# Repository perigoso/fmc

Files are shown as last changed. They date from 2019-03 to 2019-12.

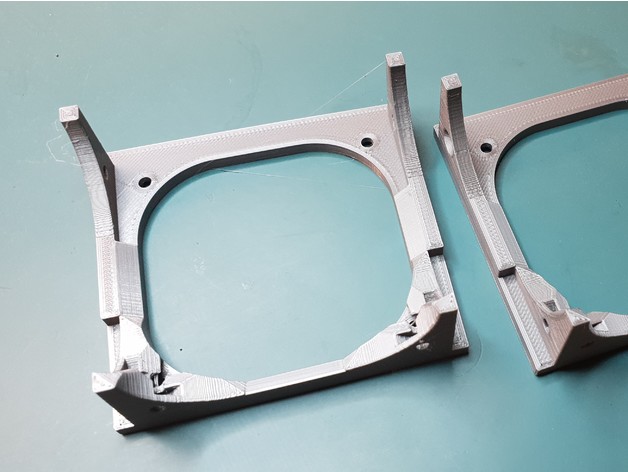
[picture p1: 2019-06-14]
hardware/mech/images/d837dd31dcf635642381db13449b711e_preview_featured.jpg

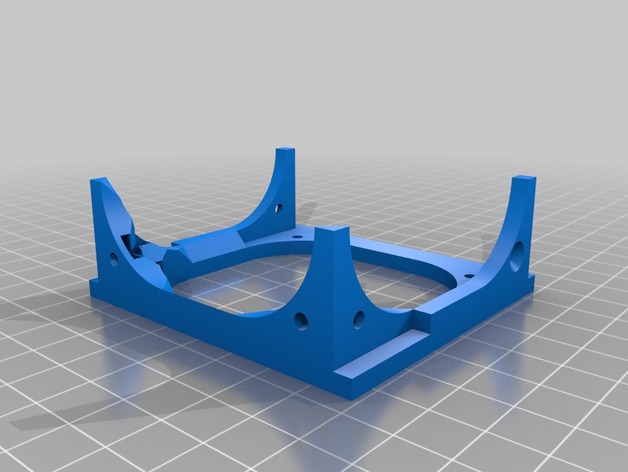
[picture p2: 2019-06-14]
hardware/mech/images/b15bb7bc5afcf96a0e5b0992fa541031_preview_featured.jpg

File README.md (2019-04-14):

# ipl motion controller

Flexible BLDC, Stepper, DC motor controller with position torque and speed control

## Authors

* **Rafael Silva** - [gimbas](https://github.com/crying-face-emoji)

See also the list of [contributors](https://github.com/gimbas/cp2130/graphs/contributors) who participated in this project.

## License

This project is licensed under the GNU General Public License v3.0 - see the [LICENSE.md](LICENSE.md) file for details

## Acknowledgments

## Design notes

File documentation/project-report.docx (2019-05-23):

Project Report

For

BLDC Motion Controller

Representative image

Company name

Date
11-Apr-19

Table of Contents

Document structure and summary

# Introduction

# Project Scope

# Project Members

Schedule Baseline and Work Breakdown

# Milestones

# Cost Breakdown

# Annotated Bibliography

- Features / system overview
- Funcional description / theory of operation
- Diagrama de blocos
- Componentes utilizados (i fix it style)
- Descrição funcionamento de componentes
- Interface / modo de controlo
- Getting started / example
- Register maps / descriptions
- Eletrical caracteristics
- Conector identification / specs

10/04/2019 - Document criation

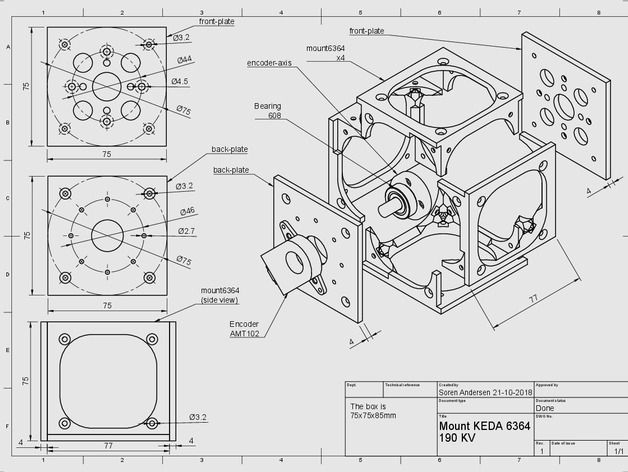
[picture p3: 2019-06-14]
hardware/mech/images/94975ee713d6cb6adc06fc9739ce1cb8_preview_featured.jpg

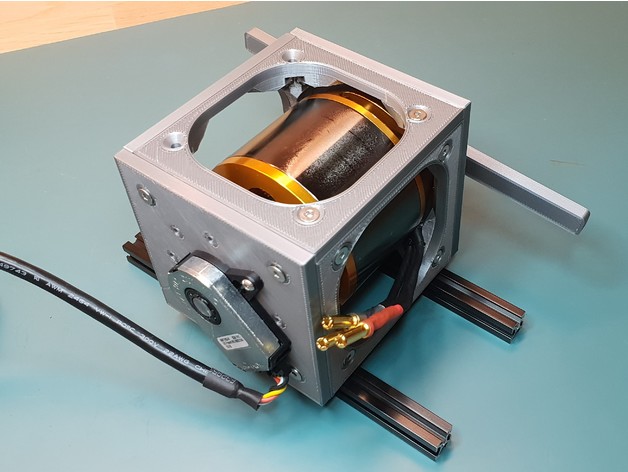
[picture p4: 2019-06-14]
hardware/mech/images/7b22074a1c9e0729f0604e04f04d98aa_preview_featured.jpg

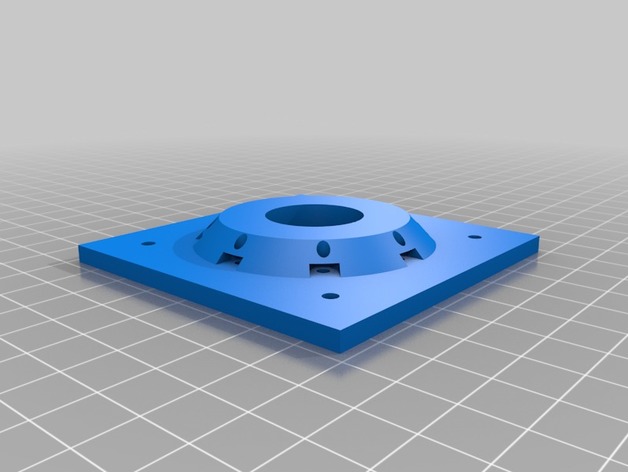
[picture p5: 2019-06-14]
hardware/mech/images/675c46c8c70f695663abe5cd2488d6a1_preview_featured.jpg

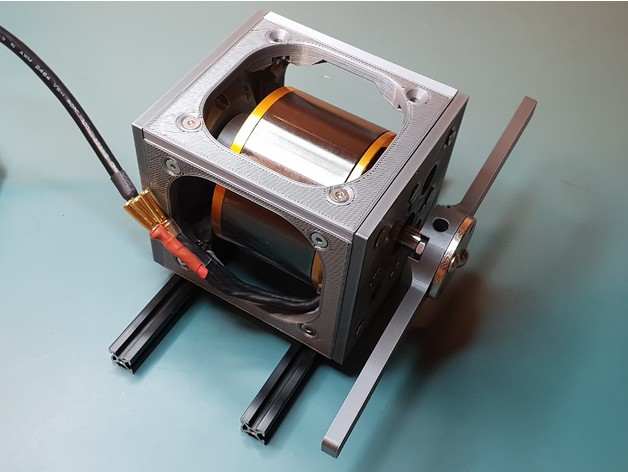
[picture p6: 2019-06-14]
hardware/mech/images/bdaeb86baf7d3e5aeb2ae743f0c55633_preview_featured.jpg

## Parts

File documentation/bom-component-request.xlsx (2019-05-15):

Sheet: Mouser
Name | Manufacturer | Reference | Description | Comments | Quantity | Link
Encoder | CUI Inc. | AMT102-V | (Kit) Rotary Encoder Incremental Programmable Quadrature with Index 2048 CPR | - | 2 | https://eu.mouser.com/ProductDetail/CUI/AMT102-V?qs=%2Fha2pyFadui4RzVBRTfUG9UOa9jox1ECIM3vJaJgYZM%3D
Schmitt Trigger Buffer | Nexperia | 74LVC3G17DP,125 | Inverters TRIP NO-INV SCH TRIG | - | 5 | https://eu.mouser.com/ProductDetail/Nexperia/74LVC3G17DP125
Headers | Hirose Connector | DF20F-10DP-1V | Headers & Wire Housings 10P M PIN HEADER DR STRAIGHT SMT GOLD | - | 1 | https://eu.mouser.com/ProductDetail/798-DF20F10DP1V55
Terminals | Phoenix Contact | 1706756 | Fixed Terminal Blocks MKDSV 5/ 4-6.35 32A | - | 3 | https://eu.mouser.com/ProductDetail/Phoenix-Contact/1710056?qs=sGAEpiMZZMvZTcaMAxB2ABBNmx7J9ErWGaY6GpdlOPw%3D
Terminals | Phoenix Contact | 1710056 | Fixed Terminal Blocks MKDSV 5/ 2-6.35 32A | - | 1 | https://eu.mouser.com/ProductDetail/Phoenix-Contact/1710056?qs=sGAEpiMZZMvZTcaMAxB2ABBNmx7J9ErWGaY6GpdlOPw%3D
Schottky Diodes | ROHM Semiconductor | BAT54SHMFHT116 | Schottky Diodes & Rectifiers 30V Vr 0.2A Io SBD SOT-23 0.1A | - | 10 | https://eu.mouser.com/ProductDetail/755-BAT54SHMFHT116
Mosfets | Infineon / IR | IRF7580MTRPBF | MOSFET 60V StrongIRFET Power Mosfet | - | 15 | https://eu.mouser.com/ProductDetail/Infineon-IR/IRF7580MTRPBF
Schottky Diodes | MCC | B5817w | Schottky Diodes & Rectifiers 1A Schottky Rectifier | - | 5 | https://eu.mouser.com/ProductDetail/833-B5817W-TP
Sense Resistors | Bourns | LRMAP3920B-R0007FT | Current Sense Resistors - SMD 1.0mOHMS 8W 1% AEC-Q200 | - | 2 | https://eu.mouser.com/ProductDetail/Bourns/CSS2H-3920R-1L00FE
NTC | Murata | NCU18WF104J60RB | NTC (Negative Temperature Coefficient) Thermistors 100kohm 1608 SMD 0.05 | - | 2 | https://eu.mouser.com/ProductDetail/Murata-Electronics/NCU18WF104J60RB
Resistors | Yageo | RC0603FR-07100RL | Thick Film Resistors 100 OHM 1% | - | 100 | https://eu.mouser.com/ProductDetail/Yageo/RC0603FR-07100RL?qs=sGAEpiMZZMvdGkrng054txdMlaQGj9fiaLtoULAqhv0%3D
Resistors | Yageo | RC0603FR-074K22L | Thick Film Resistors 4.22K OHM 1% | - | 10 | https://eu.mouser.com/ProductDetail/Yageo/RC0603FR-074K22L
Resistors | Yageo | RC0603FR-072R2L | Thick Film Resistors 2.2 OHM 1% | - | 20 | https://eu.mouser.com/ProductDetail/Yageo/RC0603FR-072R2L?qs=sGAEpiMZZMvdGkrng054t8AJgcdMkx7xQlq9a62Wvu8%3D
Resistors | Yageo | RC0603FR-0710KL | Thick Film Resistors 10K OHM 1% | - | 100 | https://eu.mouser.com/ProductDetail/Yageo/RC0603FR-0710KL
Resistors | Yageo | RC0603FR-07100KL | Thick Film Resistors 100K OHM 1% | - | 100 | https://eu.mouser.com/ProductDetail/Yageo/RC0603FR-07100KL
Capacitors | KEMET | C0603C104Z3VACTU | Multilayer Ceramic Capacitors MLCC - SMD/SMT 25V 0.1uF 0603 Y5V -20/+80% | - | 50 | https://eu.mouser.com/ProductDetail/KEMET/C0603C104Z3VACTU?qs=sGAEpiMZZMvsSlwiRhF8qiamir66WTSkBwWGHarofks%3D
Capacitors | Wurth Electronics | 885012206077 | Multilayer Ceramic Capacitors MLCC - SMD/SMT WCAP-CSGP 100pF 0603 10% 50V | - | 50 | https://eu.mouser.com/ProductDetail/Wurth-Electronics/885012206077
Capacitors | Taiyo Yuden | TMK107BJ224KAHT | Multilayer Ceramic Capacitors MLCC - SMD/SMT 0.22uF 25V X5R +/-10% 0603 AEC-Q200 | - | 5 | https://eu.mouser.com/ProductDetail/963-TMK107BJ224KAHT
Inductor | Pulse Electronics | PA4342.683ANLT | Fixed Inductors 68uH 2.4A 4mm 20% SMT | - | 2 | https://eu.mouser.com/ProductDetail/Pulse-Electronics/PA4342683ANLT
Capacitors | Lelon | VZL101M1ETR-0607 | Aluminium Electrolytic Capacitors - SMD 100uF 25 Volts 20% | - | 5 | https://eu.mouser.com/ProductDetail/Lelon/VZL101M1ETR-0607
Capacitors | Nichicon | UWT1H221MNL1GS | Aluminium Electrolytic Capacitors - SMD 50volts 220uF 10x10 '20% | - | 5 | https://eu.mouser.com/ProductDetail/Nichicon/UWT1H221MNL1GS?qs=sGAEpiMZZMtZ1n0r9vR22RxmuzErLMSVGlVEB2AeLYo%3D

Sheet: Digikey
Name | Manufacturer | Reference | Description | Comments | Quantity | Link
Motor Controller | Trinamic | TMC4671-ES | Motor Field Oriented Controller, BLDC, DC Motor, PMSM, Stepper | - | 3 | https://www.digikey.com/products/en?keywords=TMC4671-ES
Programmer cable | TagConnect | TC2050-IDC-NL-ND | Programmers Accessories | - | 1 | https://www.digikey.com/product-detail/en/tag-connect-llc/TC2050-IDC-NL/TC2050-IDC-NL-ND/2605367
tc cable clip | TagConnect | TC2050-CLIP-ND | Programmers Accessories | - | 1 | https://www.digikey.com/product-detail/en/tag-connect-llc/TC2050-CLIP/TC2050-CLIP-ND/2605374

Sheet: HobbyKing
Name | Manufacturer | Reference | Description | Comments | Quantity | Link
BLDC | KEDA | KEDA 63-64 190KV | KEDA 63-64 190KV Brushless Outrunner 10S 2000W | - | 1 | https://hobbyking.com/pt_pt/kd-53-30-high-voltage-brushless-outrunner-190kv.html

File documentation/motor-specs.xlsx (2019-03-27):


Name | Manufacturer | Reference | Hall effect | Nphase | Npole (N+S) | Stator Slots | Cogging steps / turn | velocity constant (Kv) | Ke | Kt | Imax | Pmax | Vmax | I0 (No load current) | Ri (Winding res) | Inductance | Tq | Rpm | Price | Weigth | Shaft | Body Length | Body width
KEDA 63-64 190KV Brushless Outrunner 10S 2000W | KEDA |  | N | 3 | 14 | 12 | 84 | 190 | 0.005263 | 0.005263 | 90 A | 2000 W | 37 V |  | 0 | 0 | 0.474 Nm | 4921 rpm | 45.46€ | 670g | d8mm l25mm | 66mm | 63mm
 |  |  |  |  | Copper Loss = Amps² × Rm Iron Loss = Volts × Io Motor Losses = Copper loss + Iron Loss Power In = Volts × Amps Power Out = Power In − All Losses Efficiency = Power Out / Power In Kt = 1/Kv (SI units: with RPM in rad/sec) Torque = Kt × Amps Km = Kt / sqrt(Rm)
 |  |  |  |  | Kv = RPM / (Volts × 1.414 × 0.95)
 |  |  |  |  | Kv = RPM / (Volts − Amps × Rm)

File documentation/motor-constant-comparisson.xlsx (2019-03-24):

Motor
Name | Manufacturer | reference | Sensored | kv | ke | kt | rated current | rated power | rated voltage | max torque | max rpm aproximation | price
Turnigy CA120 150kv Brushless Outrunner (100cc equiv) | Turnigy |  | N | 150 | 0.006667 | 0.006667 | 250 A | 15000 W | 70 V | 1.667 Nm | 7350 rpm | 303.19€
Turnigy RotoMax 150cc Size Brushless Outrunner Motor | Turnigy |  | N | 150 | 0.006667 | 0.006667 | 190 A | 9800 W | 52 V | 1.267 Nm | 5460 rpm | 0.00€
Turnigy CA80 160kv Brushless Outrunner (50~80cc Eq) | Turnigy |  | N | 160 | 0.006250 | 0.006250 | 200 A | 10000 W | 50 V | 1.250 Nm | 5600 rpm | 147.74€
Turnigy RotoMax 100cc Size Brushless Outrunner Motor 167kv | Turnigy |  | N | 167 | 0.005988 | 0.005988 | 170 A | 7992 W | 44 V | 1.018 Nm | 5143.6 rpm | 300.16€
Turnigy RotoMax 50cc Size Brushless Outrunner Motor | Turnigy |  | N | 172 | 0.005814 | 0.005814 | 120 A | 5300 W | 44 V | 0.698 Nm | 5297.6 rpm | 199.24€
9235-100KV Turnigy Multistar Brushless Multi-Rotor Motor | Turnigy |  | N | 100 | 0.010000 | 0.010000 | 57 A | 2800 W | 45 V | 0.570 Nm | 3150 rpm | 93.00€
Turnigy SK8 6374-149KV Sensored Brushless Motor (14P) | Turnigy |  | Y | 149 | 0.006711 | 0.006711 | 80 A | 3500 W | 44 V | 0.537 Nm | 4589.2 rpm | 86.06€
Turnigy SK8 6374-192KV Sensored Brushless Motor (14P) | Turnigy |  | Y | 192 | 0.005208 | 0.005208 | 100 A | 4400 W | 45 V | 0.521 Nm | 6048 rpm | 85.90€
Turnigy SK8 6374-130KV Sensored Brushless Motor (14P) | Turnigy |  | Y | 130 | 0.007692 | 0.007692 | 65 A | 2800 W | 45 V | 0.500 Nm | 4095 rpm | 85.69€
KEDA 63-64 190KV Brushless Outrunner 10S 2000W | KEDA |  | N | 190 | 0.005263 | 0.005263 | 90 A | 2000 W | 37 V | 0.474 Nm | 4921 rpm | 45.46€
Turnigy Aerodrive SK3 - 6374-149KV Brushless Outrunner Motor | Turnigy |  | N | 149 | 0.006711 | 0.006711 | 70 A | 2250 W | 44 V | 0.470 Nm | 4589.2 rpm | 86.21€
Turnigy Aerodrive SK3 - 6374-168KV Brushless Outrunner Motor | Turnigy |  | N | 168 | 0.005952 | 0.005952 | 70 A | 2400 W | 44 V | 0.417 Nm | 5174.4 rpm | 74.88€
Turnigy Aerodrive SK3 - 6374-192KV Brushless Outrunner Motor | Turnigy |  | N | 192 | 0.005208 | 0.005208 | 80 A | 2750 W | 44 V | 0.417 Nm | 5913.6 rpm | 74.77€
KEDA 56-63 195KV Brushless Outrunner 6S 1500W | KEDA |  | N | 195 | 0.005128 | 0.005128 | 80 A | 1500 W | 22 V | 0.410 Nm | 3003 rpm | 36.92€
9225-90KV Turnigy Multistar Brushless Multi-Rotor Motor | Turnigy |  | N | 90 | 0.011111 | 0.011111 | 36 A | 1200 W | 45 V | 0.400 Nm | 2835 rpm | 148.72€
Turnigy SK8 6364-110KV Sensored Brushless Motor (14P) | Turnigy |  | Y | 110 | 0.009091 | 0.009091 | 40 A | 1750 W | 45 V | 0.364 Nm | 3465 rpm | 80.39€
Turnigy D5035-125KV Sensored Brushless Motor | Turnigy |  | Y | 125 | 0.008000 | 0.008000 | 45 A | 2000 W | 44 V | 0.360 Nm | 3850 rpm | 91.41€
Turnigy RotoMax 1.60 Brushless Outrunner Motor | Turnigy |  | N | 231 | 0.004329 | 0.004329 | 80 A | 2960 W | 37 V | 0.346 Nm | 5982.9 rpm | 121.94€
Turnigy Aerodrive SK3 - 6364-190KV Brushless Outrunner Motor | Turnigy |  | N | 190 | 0.005263 | 0.005263 | 65 A | 2450 W | 37 V | 0.342 Nm | 4921 rpm | 78.97€
PROPDRIVE v2 5060 270KV Brushless Outrunner Motor | PROPDRIVE |  | N | 270 | 0.003704 | 0.003704 | 90 A | 2400 W | 30 V | 0.333 Nm | 5670 rpm | 49.94€
Turnigy SK8 6364-245KV Sensored Brushless Motor (14P) | Turnigy |  | Y | 245 | 0.004082 | 0.004082 | 80 A | 3500 W | 45 V | 0.327 Nm | 7717.5 rpm | 80.39€
Turnigy SK8 6364-190KV Sensored Brushless Motor (14P) | Turnigy |  | Y | 190 | 0.005263 | 0.005263 | 60 A | 2600 W | 45 V | 0.316 Nm | 5985 rpm | 80.39€
Turnigy Aerodrive SK3 - 6364-213KV Brushless Outrunner Motor | Turnigy |  | N | 213 | 0.004695 | 0.004695 | 65 A | 2550 W | 37 V | 0.305 Nm | 5516.7 rpm | 66.09€
9225-160KV Turnigy Multistar Brushless Multi-Rotor Motor | Turnigy |  | N | 160 | 0.006250 | 0.006250 | 48 A | 1200 W | 35 V | 0.300 Nm | 3920 rpm | 93.00€
Turnigy SK8 6354-140KV Sensored Brushless Motor (14P) | Turnigy |  | Y | 140 | 0.007143 | 0.007143 | 42 A | 1850 W | 45 V | 0.300 Nm | 4410 rpm | 71.06€
Turnigy Aerodrive SK3 - 6364-245Kv Brushless Outrunner Motor | Turnigy |  | N | 245 | 0.004082 | 0.004082 | 70 A | 2700 W | 37 V | 0.286 Nm | 6345.5 rpm | 70.57€
Turnigy SK8 6354-200KV Sensored Brushless Motor (14P) | Turnigy |  | Y | 200 | 0.005000 | 0.005000 | 55 A | 2420 W | 45 V | 0.275 Nm | 6300 rpm | 71.14€
Turnigy Aerodrive SK3 - 6354-260KV Brushless Outrunner Motor | Turnigy |  | N | 260 | 0.003846 | 0.003846 | 70 A | 2360 W | 37 V | 0.269 Nm | 6734 rpm | 67.20€
Turnigy SK8 6354-260KV Sensored Brushless Motor (14P) | Turnigy |  | Y | 260 | 0.003846 | 0.003846 | 70 A | 3000 W | 45 V | 0.269 Nm | 8190 rpm | 70.66€
Turnigy G160 Brushless Outrunner 290kv (160 Glow) | Turnigy |  | N | 290 | 0.003448 | 0.003448 | 78 A | 2700 W | 37 V | 0.269 Nm | 7511 rpm | 84.26€
Turnigy Aerodrive SK3 - 5065-236Kv Brushless Outrunner Motor | Turnigy |  | N | 236 | 0.004237 | 0.004237 | 60 A | 1850 W | 37 V | 0.254 Nm | 6112.4 rpm | 61.32€
PROPDRIVE v2 5060 380KV Brushless Outrunner Motor | PROPDRIVE |  | N | 380 | 0.002632 | 0.002632 | 90 A | 2665 W | 36 V | 0.237 Nm | 9576 rpm | 42.13€
Turnigy Aerodrive SK3 - 5065-275KV Brushless Outrunner Motor | Turnigy |  | N | 275 | 0.003636 | 0.003636 | 65 A | 2050 W | 37 V | 0.236 Nm | 7122.5 rpm | 53.16€
Turnigy Aerodrive SK3 - 5065-320kv Brushless Outrunner Motor | Turnigy |  | N | 320 | 0.003125 | 0.003125 | 70 A | 2220 W | 37 V | 0.219 Nm | 8288 rpm | 56.64€
Turnigy G60 Brushless Outrunner 300kv (.60 Glow) | Turnigy |  | N | 300 | 0.003333 | 0.003333 | 65 A | 1425 W | 26 V | 0.217 Nm | 5460 rpm | 50.08€
Turnigy Aerodrive SK3 - 5055-280KV Brushless Outrunner Motor | Turnigy |  | N | 280 | 0.003571 | 0.003571 | 60 A | 1510 W | 37 V | 0.214 Nm | 7252 rpm | 53.02€
Turnigy Aerodrive SK3 - 5055-320Kv Brushless Outrunner Motor | Turnigy |  | N | 320 | 0.003125 | 0.003125 | 65 A | 1650 W | 37 V | 0.203 Nm | 8288 rpm | 53.11€
Turnigy Aerodrive SK3 - 5055-380KV Brushless Outrunner Motor | Turnigy |  | N | 380 | 0.002632 | 0.002632 | 65 A | 1600 W | 37 V | 0.171 Nm | 9842 rpm | 43.29€
Turnigy Aerodrive SK3 - 5055-430KV Brushless Outrunner Motor | Turnigy |  | N | 430 | 0.002326 | 0.002326 | 70 A | 1750 W | 30 V | 0.163 Nm | 9030 rpm | 46.03€
Turnigy G60 Brushless Outrunner 400kv (.60 Glow) | Turnigy |  | N | 400 | 0.002500 | 0.002500 | 65 A | 1009 W | 26 V | 0.163 Nm | 7280 rpm | 53.29€
Turnigy Aerodrive SK3 - 4250-350KV Brushless Outrunner Motor | Turnigy |  | N | 350 | 0.002857 | 0.002857 | 53 A | 1190 W | 19 V | 0.151 Nm | 4655 rpm | 34.04€
Turnigy Aerodrive SK3 - 4250-410KV Brushless Outrunner Motor | Turnigy |  | N | 410 | 0.002439 | 0.002439 | 55 A | 1310 W | 19 V | 0.134 Nm | 5453 rpm | 34.04€
Turnigy G46 Brushless Outrunner 420kv (.46 Glow) | Turnigy |  | N | 420 | 0.002381 | 0.002381 | 55 A | 925 W | 19 V | 0.131 Nm | 5586 rpm | 46.44€
4112-320KV Turnigy Multistar 22 Pole Brushless Multi-Rotor Motor With Extra Long Leads | Turnigy |  | N | 320 | 0.003125 | 0.003125 | 20 A | 660 W | 30 V | 0.062 Nm | 6720 rpm | 37.18€
Multistar Elite 3508-268kv Multi-Rotor Motor with NMB Bearings | Turnigy |  | N | 268 | 0.003731 | 0.003731 | 16 A | 400 W | 22.2 V | 0.060 Nm | 4164.72 rpm | 31.12€
4010-375KV Turnigy Multistar 22 Pole Brushless Multi-Rotor Motor With Extra Long Leads | Turnigy |  | N | 375 | 0.002667 | 0.002667 | 20 A | 450 W | 25 V | 0.053 Nm | 6562.5 rpm | 38.49€
Quanum MT Series 5206 320KV Brushless Multirotor Motor Built by DYS | DYS |  | N | 320 | 0.003125 | 0.003125 | 17 A | 384 W | 22 V | 0.053 Nm | 4928 rpm | 33.50€
Quanum MT Series 4108 370KV Brushless Multirotor Motor Built by DYS | DYS |  | N | 370 | 0.002703 | 0.002703 | 16 A | 355 W | 22 V | 0.043 Nm | 5698 rpm | 30.38€
Multistar Elite 3510-350kv Carbon Case Multi-Rotor Motor | Turnigy |  | N | 350 | 0.002857 | 0.002857 | 15 A | 330 W | 22 V | 0.043 Nm | 5390 rpm | 35.35€
Turnigy Multistar 4822-390Kv 22Pole Multi-Rotor Outrunner | Turnigy |  | N | 390 | 0.002564 | 0.002564 | 15 A | 300 W | 22 V | 0.038 Nm | 6006 rpm | 34.22€
Turnigy Multistar 4225-390Kv 16Pole Multi-Rotor Outrunner | Turnigy |  | N | 390 | 0.002564 | 0.002564 | 15 A | 330 W | 22 V | 0.038 Nm | 6006 rpm | 31.77€
 |  |  |  |  | #DIV/0! | #DIV/0! |  |  |  | #DIV/0! | 0 rpm | 0.00€

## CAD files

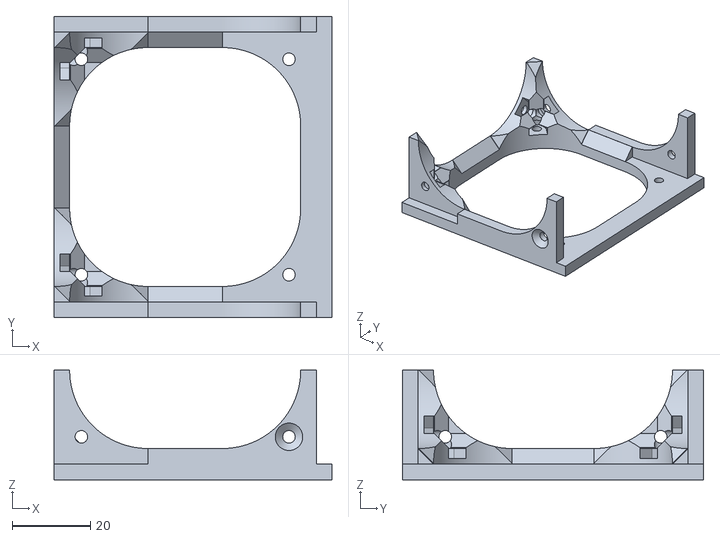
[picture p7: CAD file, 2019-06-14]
hardware/mech/files/v25-mount6364-rotated.stl
71.0 x 77.0 x 28.0

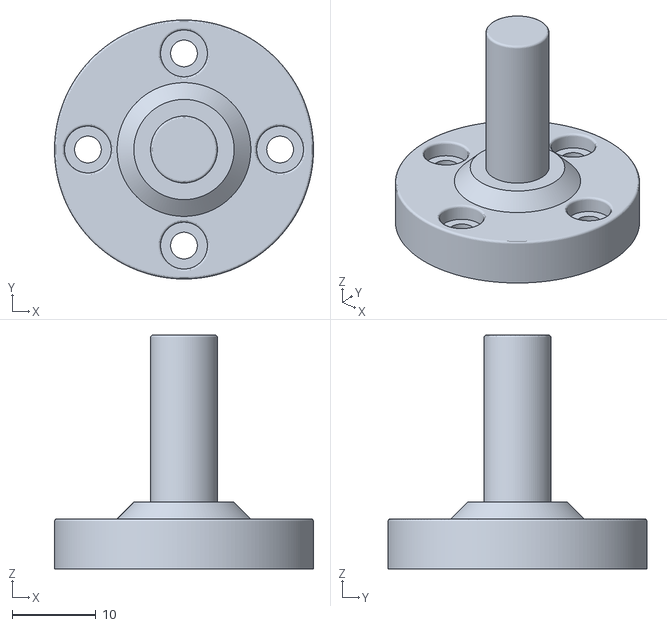
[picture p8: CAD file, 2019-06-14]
hardware/mech/files/v25-encoder-axis.stl
31.0 x 31.0 x 28.0

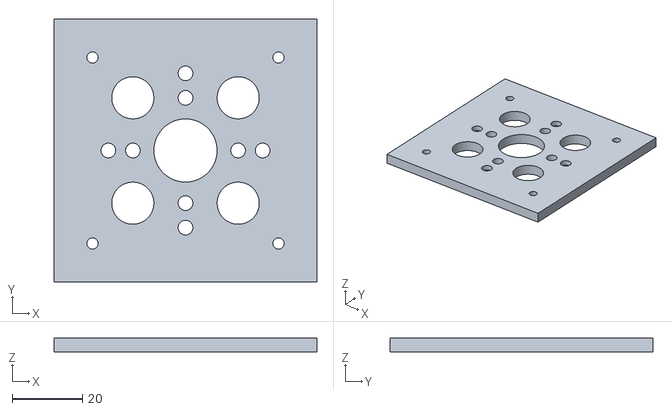
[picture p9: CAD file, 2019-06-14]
hardware/mech/files/v25-front-plate.stl
75.0 x 75.0 x 4.00

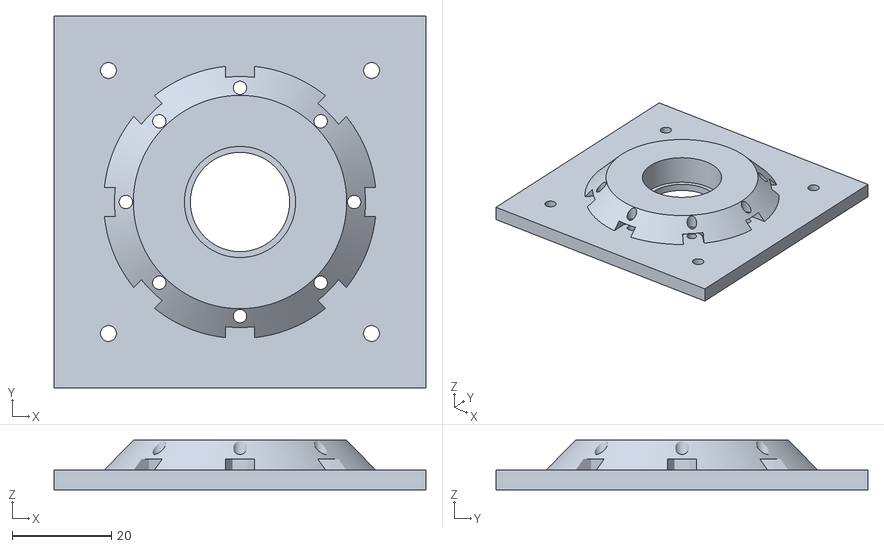
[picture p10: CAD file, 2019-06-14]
hardware/mech/files/v25-back-plate-rotated.stl
75.0 x 75.0 x 10.0

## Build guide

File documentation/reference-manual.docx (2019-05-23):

Project Report

For

BLDC Motion Controller

Representative image

Company name

Date
11-Apr-19

Table of Contents

# Introduction

# Project Scope

# Project Members

# Milestones

- Capa
- About this document
- Table of Contents
- Introdução
- Features / system overview
- Funcional description / theory of operation
- Diagrama de blocos
- Componentes utilizados (i fix it style)
- Descrição funcionamento de componentes
- Interface / modo de controlo
- Getting started / example
- Register maps / descriptions
- Eletrical caracteristics
- Conector identification / specs
- Revision history
- “Bibliografia”

10/04/2019 - Document criation

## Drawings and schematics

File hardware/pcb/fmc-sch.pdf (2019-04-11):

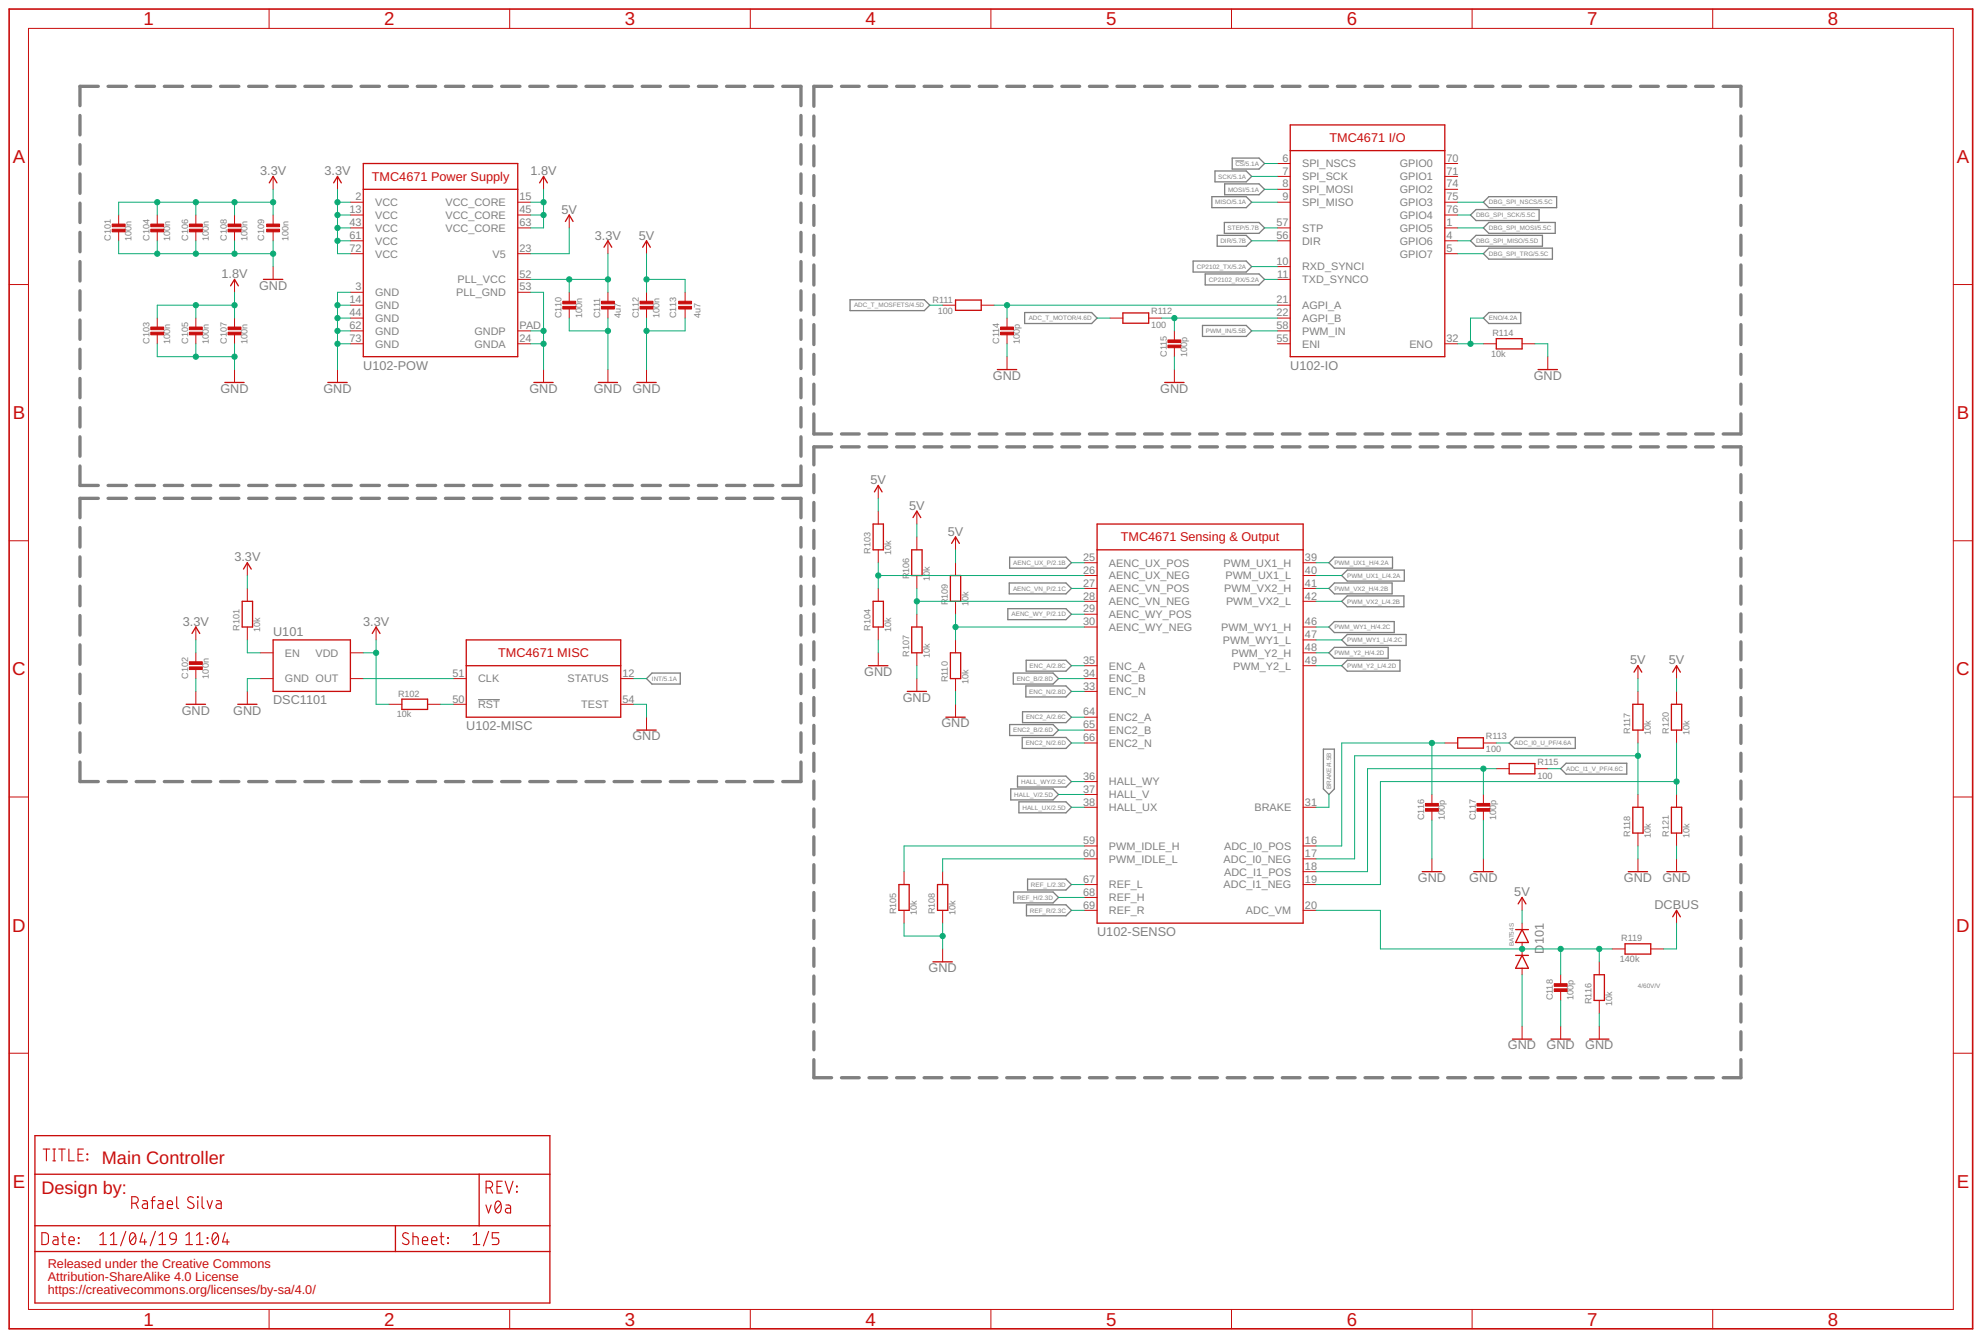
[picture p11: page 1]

13 | 45
43 | 63
61 | 23

14 | PAD

Released under the Creative Commons https://creativecommons.org/licenses/by-sa/4.0/
Attribution-ShareAlike 4.0 License

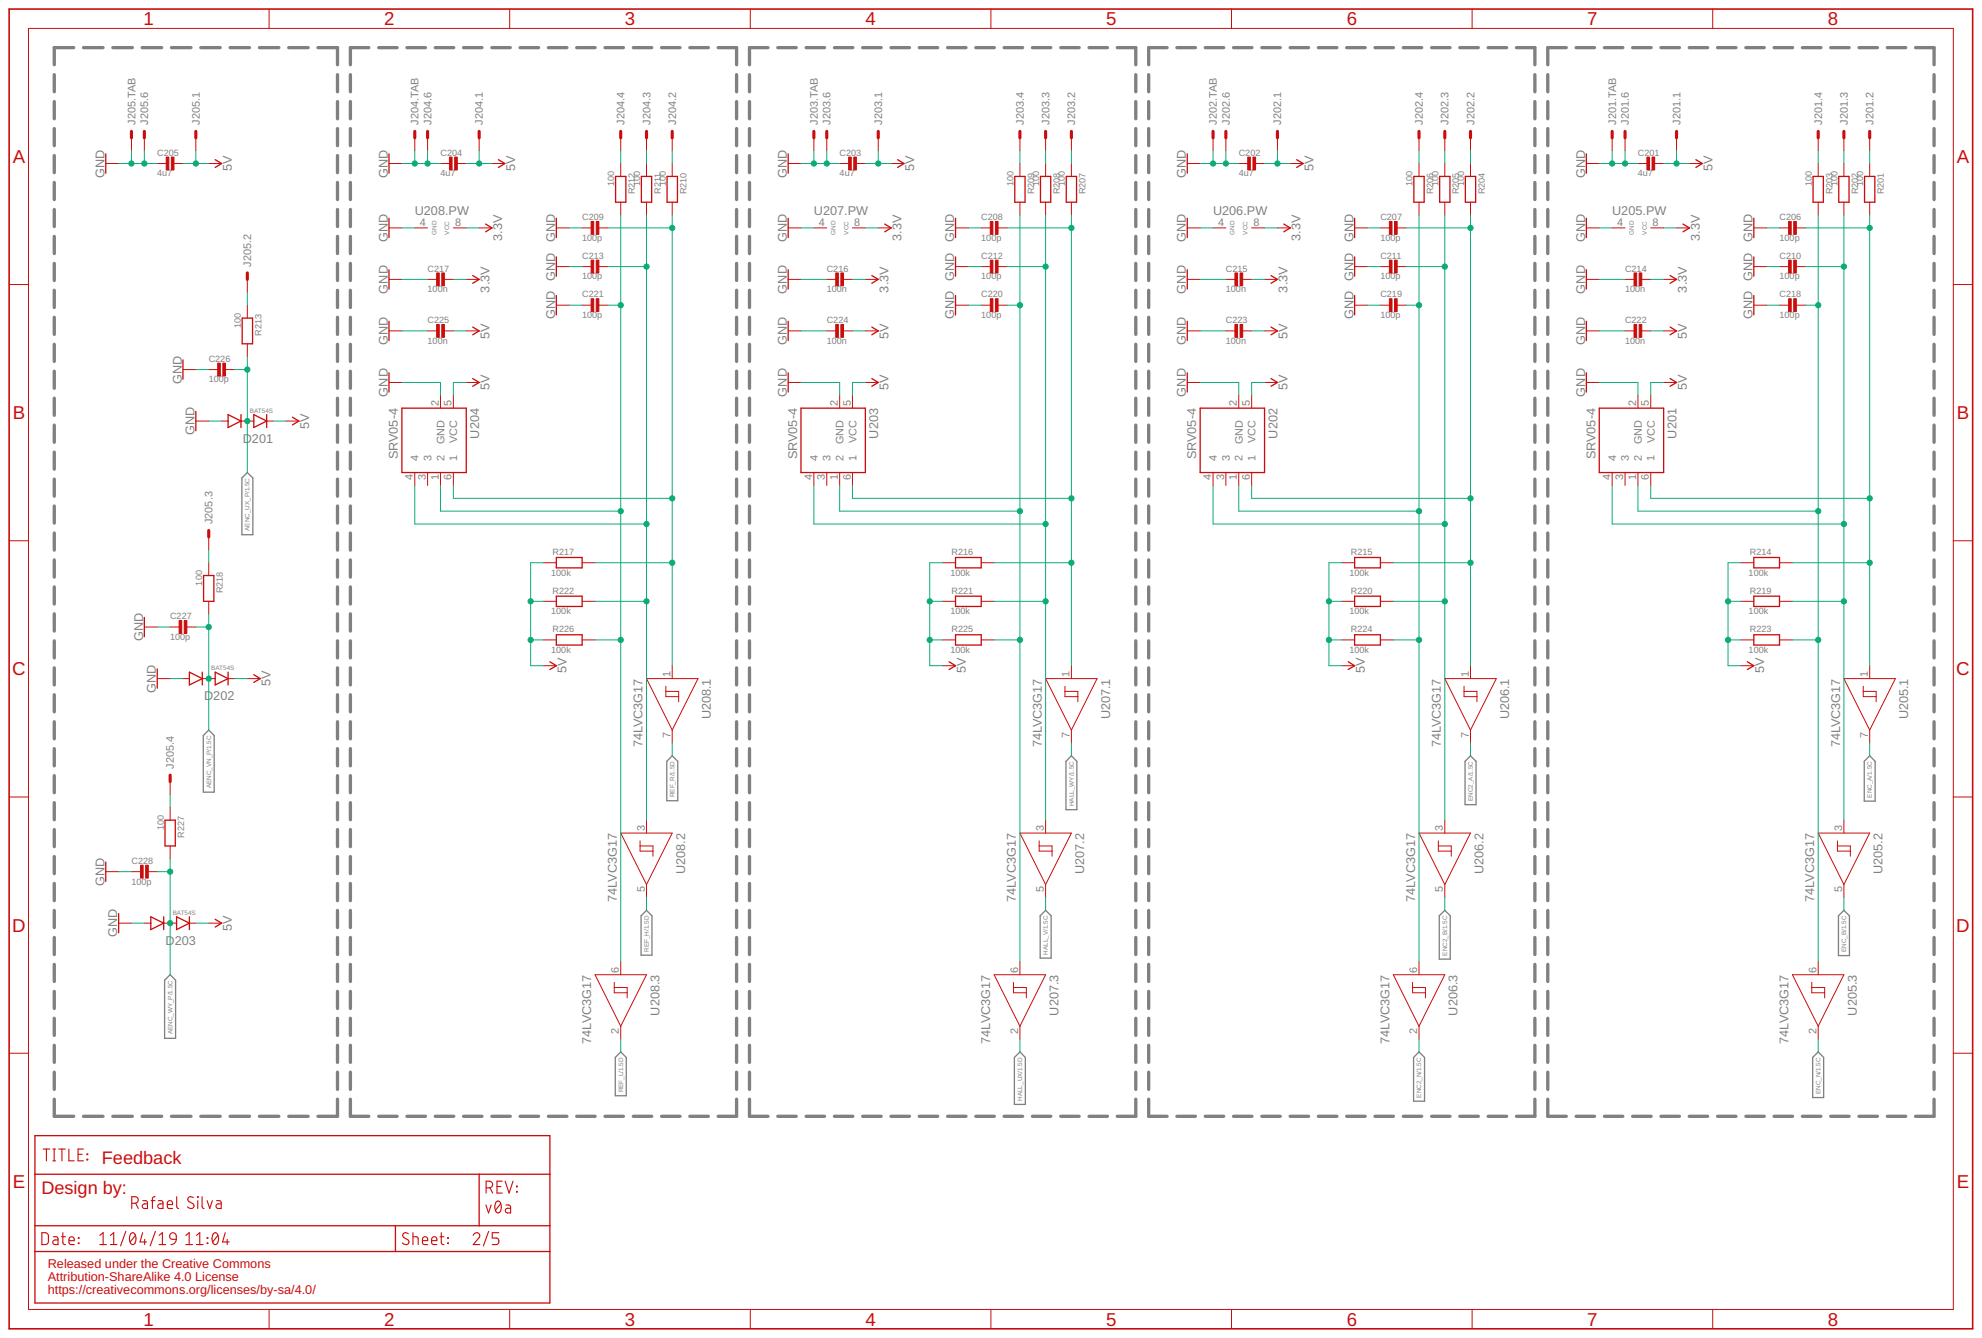
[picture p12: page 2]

VCC GND VCC GND VCC GND VCC GND 74LVC3G17 74LVC3G17 74LVC3G17 100 100 100 100p 100p 100p 4u7 5V GND GND GND GND GND 5V GND 74LVC3G17 74LVC3G17 74LVC3G17 100 100 100 100p 100p 100p 4u7 5V GND GND GND GND GND 5V GND 74LVC3G17 74LVC3G17 74LVC3G17 100 100 100 100p 100p 100p 4u7 5V GND GND GND GND GND 5V GND 100n 5V GND 3.3V 3.3V G100n ND 3.3V 100n 5V GND G100n ND 3.3V 3.3V 100k 100k 100k5V 100k 100k 100k5V 100k 100k 100k5V 100n 5V GND G100n ND 3.3V 74LVC3G17 74LVC3G17 74LVC3G17 100 100 100 100p 100p 100p 4u7 5V GND GND GND GND GND 5V GND 100n 5V GND G100n ND 3.3V 3.3V 100k 100k 100k5V BAT54S BAT54S BAT54S 100p 100p 100p 100 100 100 4u7 5V GND GND GND GND 5V 5V 5V GND GND GND SRV05-4 SRV05-4 SRV05-4 SRV05-4 1 7 U205.1 3 5 U205.2 6 2 U205.3 4 8 U205.PW J201.1 J201.2 J201.3 J201.4 J201.6 J201.TAB R201 R202 R203 C206 C210 C218 C201 1 7 U206.1 3 5 U206.2 6 2 U206.3 4 8 U206.PW J202.1 J202.2 J202.3 J202.4 J202.6 J202.TAB R204 R205 R206 C207 C211 C219 C202 1 7 U207.1 3 5 U207.2 6 2 U207.3 4 8 U207.PW J203.1 J203.2 J203.3 J203.4 J203.6 J203.TAB R207 R208 R209 C208 C212 C220 C203 C223 C215 C224 C216 R216 R221 R225 R215 R220 R224 R214 R219 R223 C222 C214 1 7 U208.1 3 5 U208.2 6 2 U208.3 4 8 U208.PW J204.1 J204.2 J204.3 J204.4 J204.6 J204.TAB R210 R211 R212 C209 C213 C221 C204 C225 C217 R217 R222 R226 D201 D202 D203 C226 C227 C228 R213 R218 R227 C205 J205.1 J205.2 J205.3 J205.4 J205.6 J205.TAB VCC 5 GND 2 1 6 2 1 3 3 4 4 U202 VCC 5 GND 2 1 6 2 1 3 3 4 4 U201 VCC 5 GND 2 1 6 2 1 3 3 4 4 U203 VCC 5 GND 2 1 6 2 1 3 3 4 4 U204 ENC2_A/1.5C ENC2_B/1.5C ENC2_N/1.5C HALL_WY/1.5C HALL_V/1.5C HALL_UX/1.5D ENC_A/1.5C ENC_B/1.5C ENC_N/1.5C REF_R/1.5D REF_H/1.5D REF_L/1.5D AENC_UX_P/1.5C AENC_VN_P/1.5C AENC_WY_P/1.5C Feedback ABCDE 1 2 3 4 5 6 7 8 ABCDE 1 2 3 4 5 6 7 8 Design by: Released under the Creative Commons https://creativecommons.org/licenses/by-sa/4.0/ Attribution-ShareAlike 4.0 License

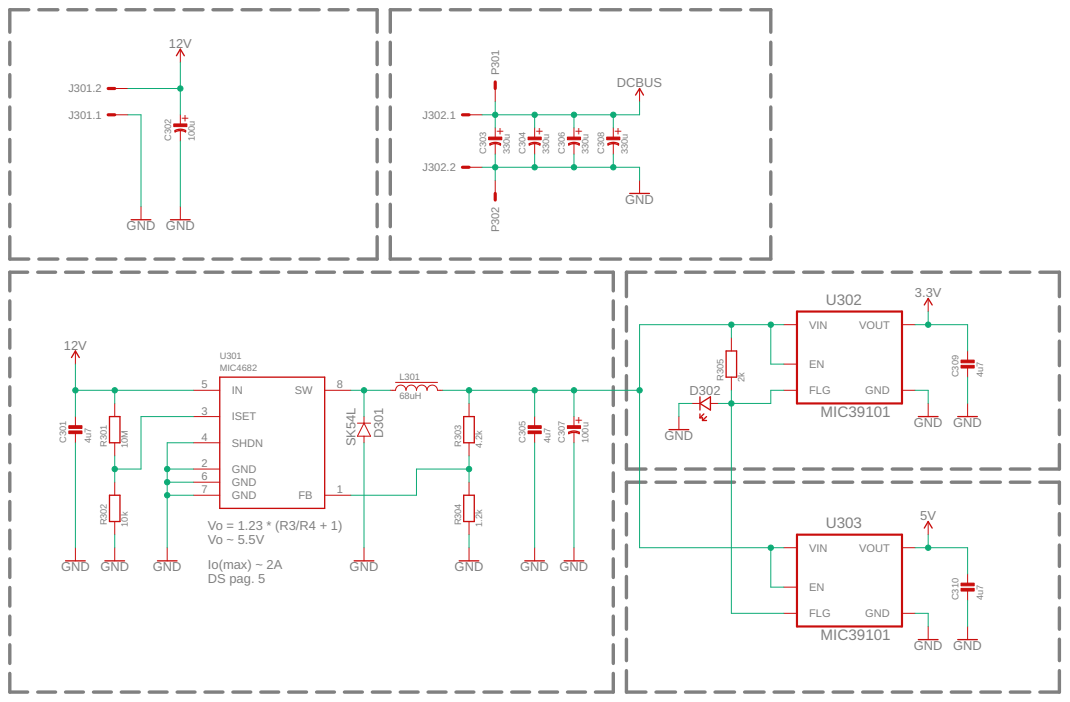
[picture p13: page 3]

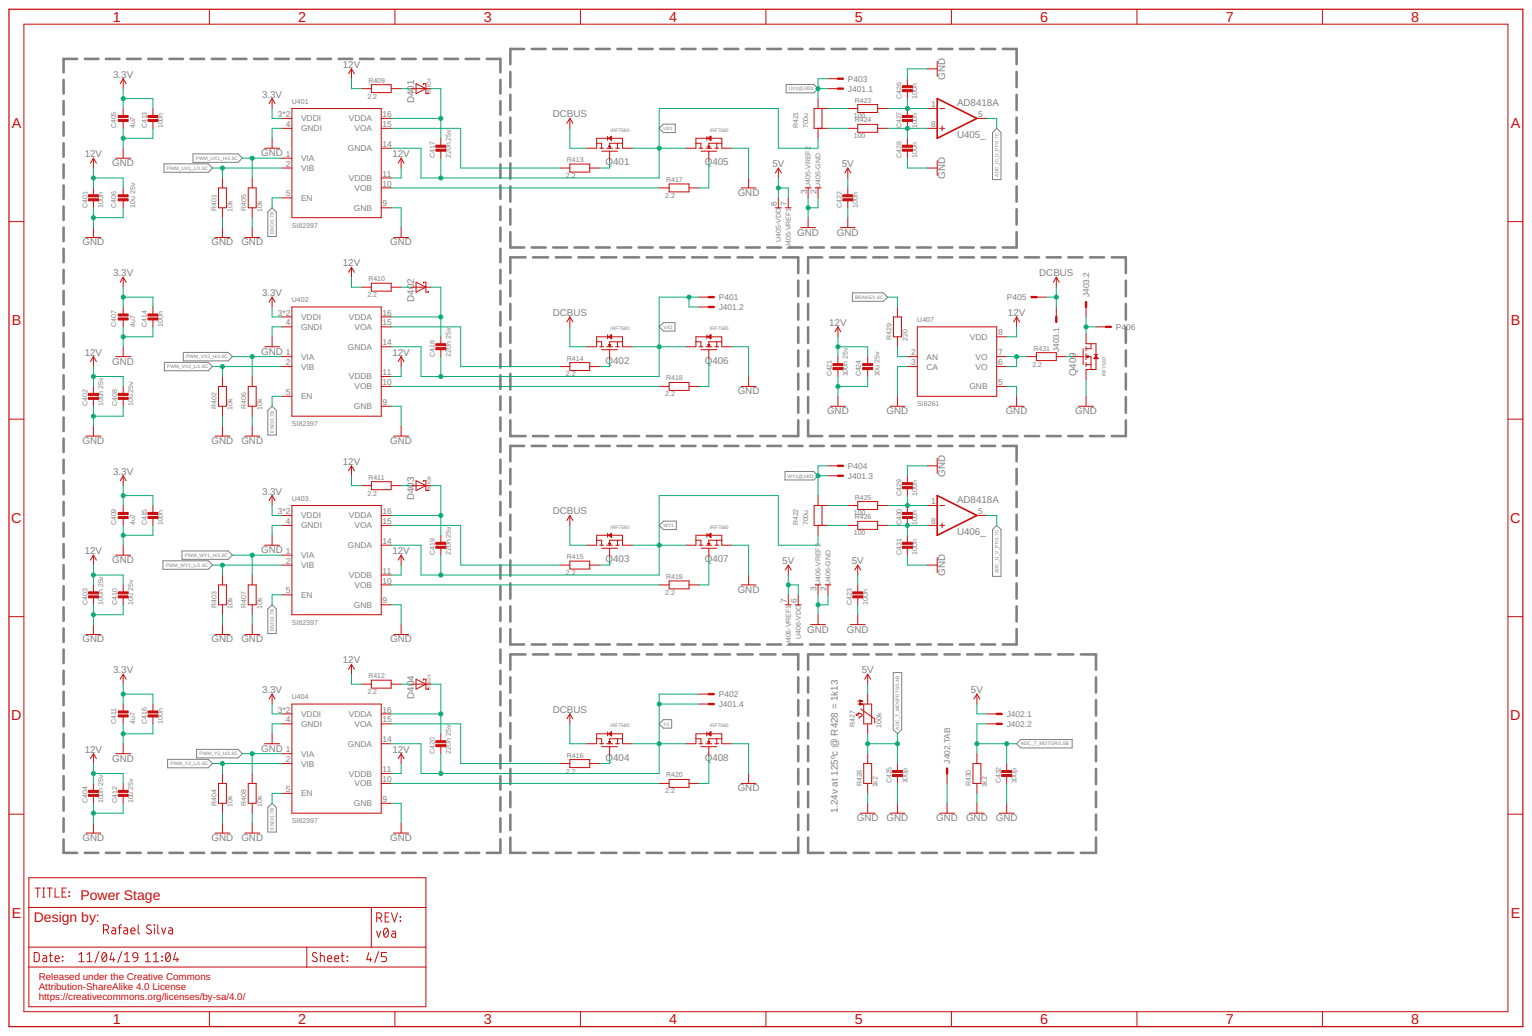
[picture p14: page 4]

1.24v at 125ºc @ R428 = 1k13 GND DCBUS GND 220n 25v 12V DSK24 IRF7580 IRF7580 12V GND DCBUS GND 220n 25v 12V IRF7580 IRF7580 12V GND DCBUS GND 220n 25v 12V DSK24 IRF7580 IRF7580 12V GND DCBUS GND 220n 25v 12V DSK24 IRF7580 IRF7580 12V 3.3V GND 100n 100n 10u 25v 4u7 3.3V GND GND 12V 100n 100n 25v 10u 25v 4u7 3.3V GND GND 12V 100n 100n 25v 10u 25v 4u7 3.3V GND GND 12V 100n 100n 25v 10u 25v 4u7 3.3V GND GND 12V 3.3V GND 3.3V GND 3.3V GND 2.2 2.2 2.2 2.2 2.2 2.2 2.2 2.2 GND 5V 5V GND100n GND 5V 5V GND100n 10k 10k GND GND10k 10k GND GND10k 10k GND GND10k 10k GND GND 2.2 2.2 2.2 2.2 700u 700u GND 5V 1k2 1k2 GND 5V GND GND 100k GND IRF7580 2.2 GND DCBUS 12V GND 220 GND 100n 25v GND 12V 10u 25v 100p 100p 100 100 100n 100n 100n GND GND 100 100 100n 100n 100n GND GND AD8418A AD8418A VDDI 3*2 GNDI 4 VIA 1 VIB 2 EN 5 VOB 10 GNB 9 VDDB 11 GNDA 14 VOA 15 VDDA 16 U401 SI82397 C417 D401 Q401 Q405 VDDI 3*2 GNDI 4 VIA 1 VIB 2 EN 5 VOB 10 GNB 9 VDDB 11 GNDA 14 VOA 15 VDDA 16 U402 SI82397 C418 D402 Q402 Q406 VDDI 3*2 GNDI 4 VIA 1 VIB 2 EN 5 VOB 10 GNB 9 VDDB 11 GNDA 14 VOA 15 VDDA 16 U403 SI82397 C419 D403 Q403 Q407 VDDI 3*2 GNDI 4 VIA 1 VIB 2 EN 5 VOB 10 GNB 9 VDDB 11 GNDA 14 VOA 15 VDDA 16 U404 SI82397 C420 D404 Q404 Q408 C413 C401 C406 C405 C414 C402 C408 C407 C415 C403 C410 C409 C416 C404 C412 C411 R413 R417 R414 R418 R415 R419 R416 R420 C422 C423 R405 R401 R406 R402 R407 R403 R408 R404 R409 R410 R411 R412 R421 R422 R428 R430 R427J402.1 J402.2 J402.TAB Q409 R431 AN 2 CA 3 GNB 5 VO 6 VO 7 VDD 8 U407 SI8261 R429 C421 C424 C432 C425 J401.1 J401.2 J401.3 J401.4 P403 P401 P404 P402 R423 R424 C427 C426 C428 R425 R426 C430 C429 C431 81 5 U405_ 2 U405-GND 3 U405-VREF2 6 U405-VDD 7 U405-VREF1 81 5 U406_ 2 U406-GND 3 U406-VREF2 6 U406-VDD 7 U406-VREF1 J403.1 J403.2 P405 P406 UX1 VX2 WY1 Y2 PWM_UX1_H/1.6C PWM_UX1_L/1.6C ENO/1.7B ENO/1.7B ENO/1.7B ENO/1.7B PWM_VX2_H/1.6C PWM_VX2_L/1.6C PWM_WY1_H/1.6C PWM_WY1_L/1.6C PWM_Y2_H/1.6C PWM_Y2_L/1.6C UX1@J401 ADC_I0_U_PF/1.7C ADC_I1_V_PF/1.7C ADC_T_MOSFETS/1.4B ADC_T_MOTOR/1.5B BRAKE/1.6C WY1@J401 Power Stage ABCDE 1 2 3 4 5 6 7 8 ABCDE 1 2 3 4 5 6 7 8 Design by: Released under the Creative Commons https://creativecommons.org/licenses/by-sa/4.0/ Attribution-ShareAlike 4.0 License

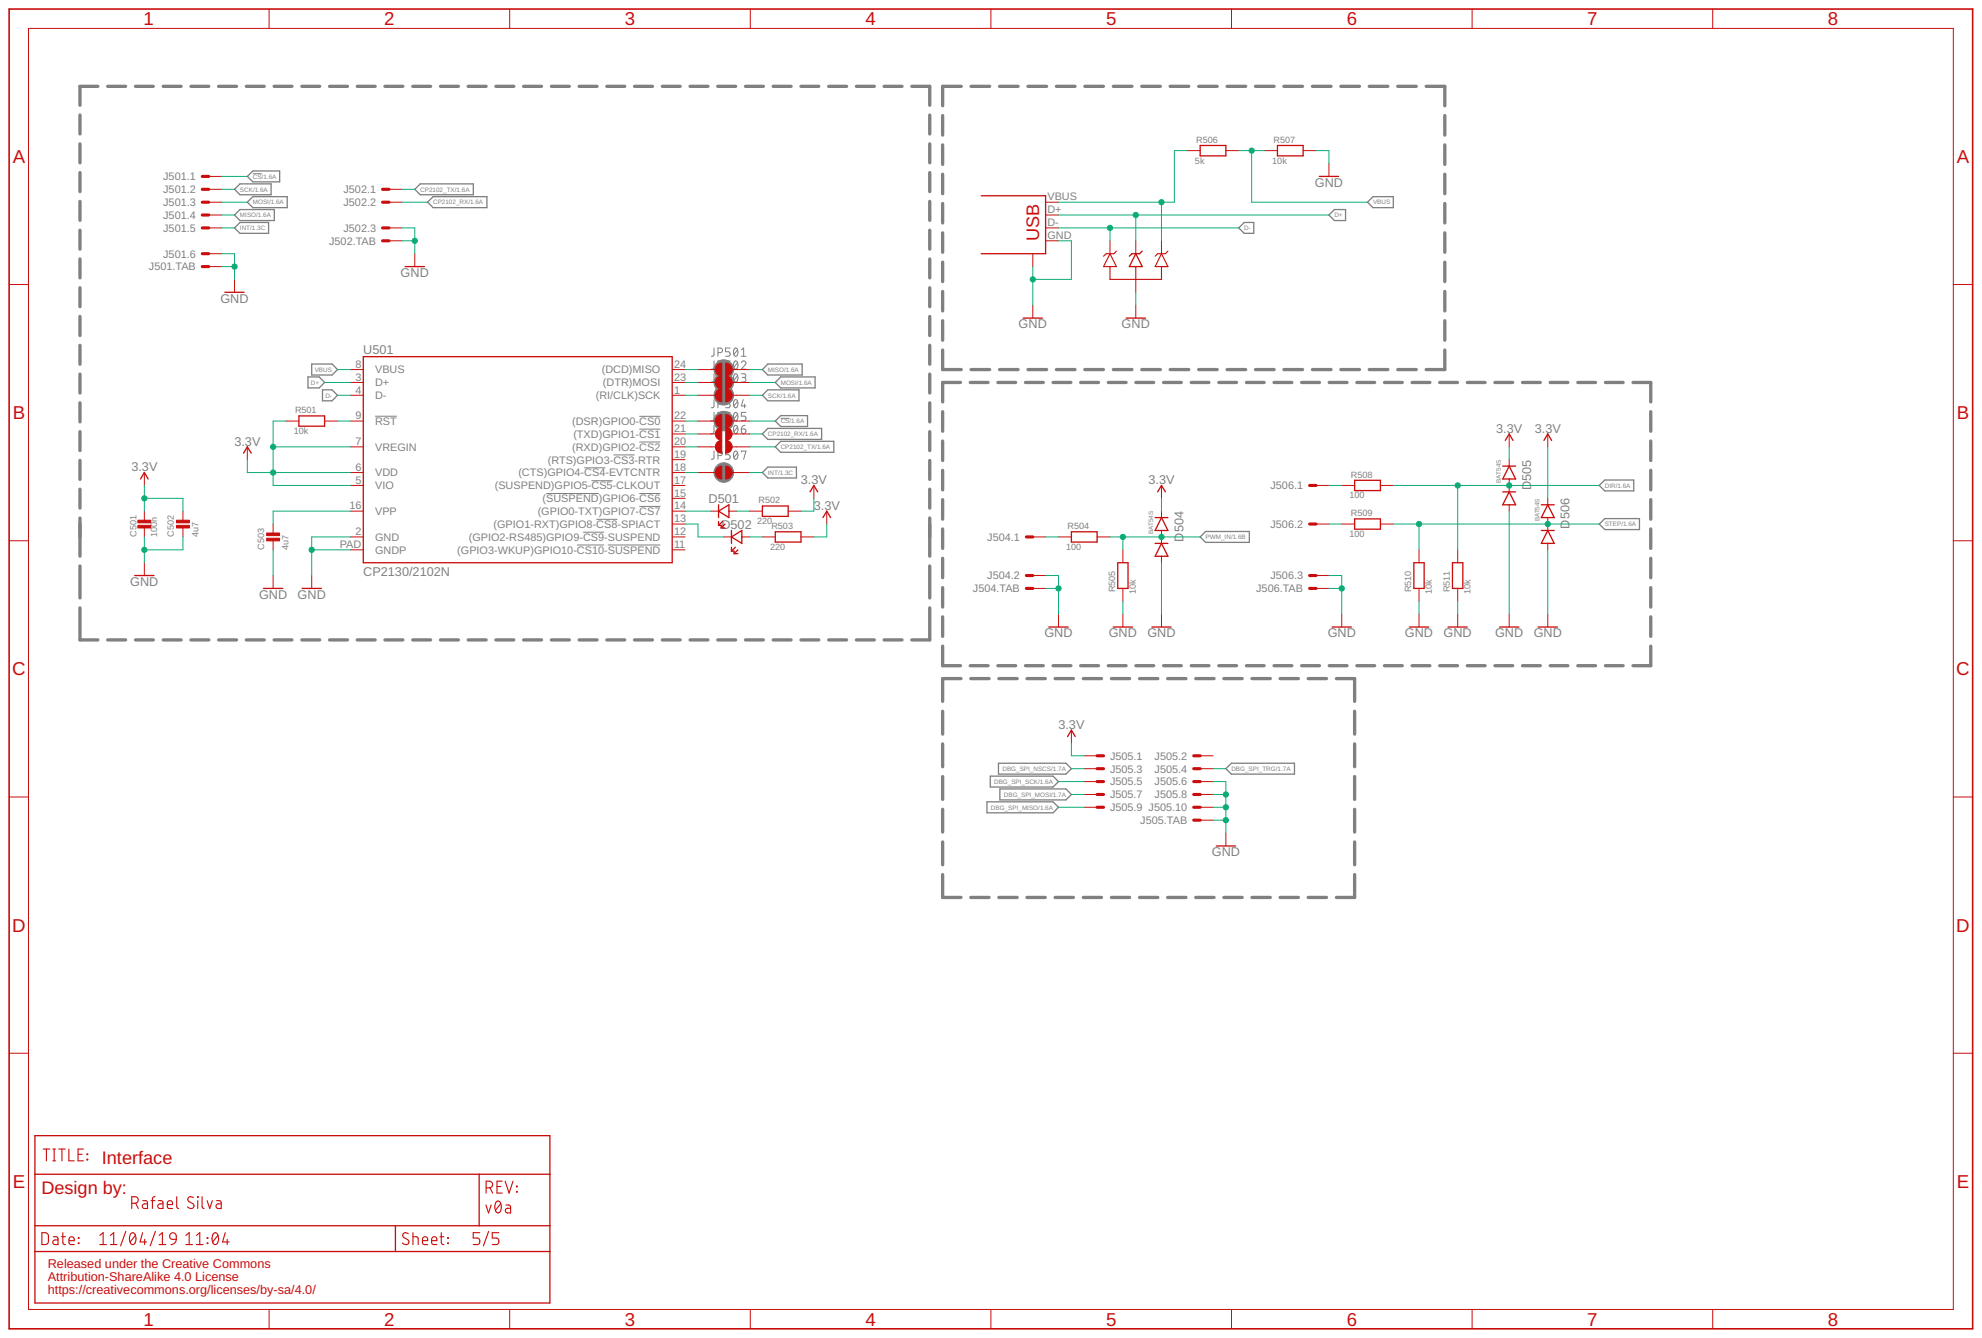
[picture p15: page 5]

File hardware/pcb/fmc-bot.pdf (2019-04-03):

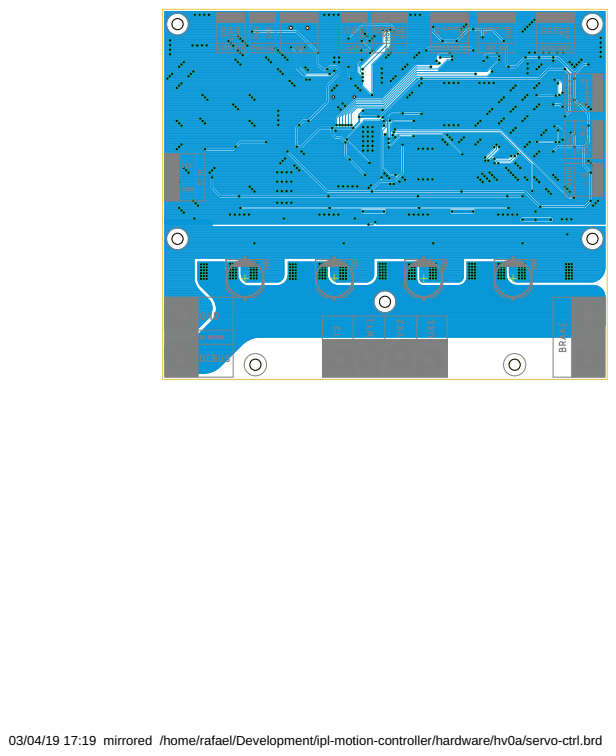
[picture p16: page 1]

03/04/19 17:19 mirrored /home/rafael/Development/ipl-motion-controller/hardware/hv0a/servo-ctrl.brd

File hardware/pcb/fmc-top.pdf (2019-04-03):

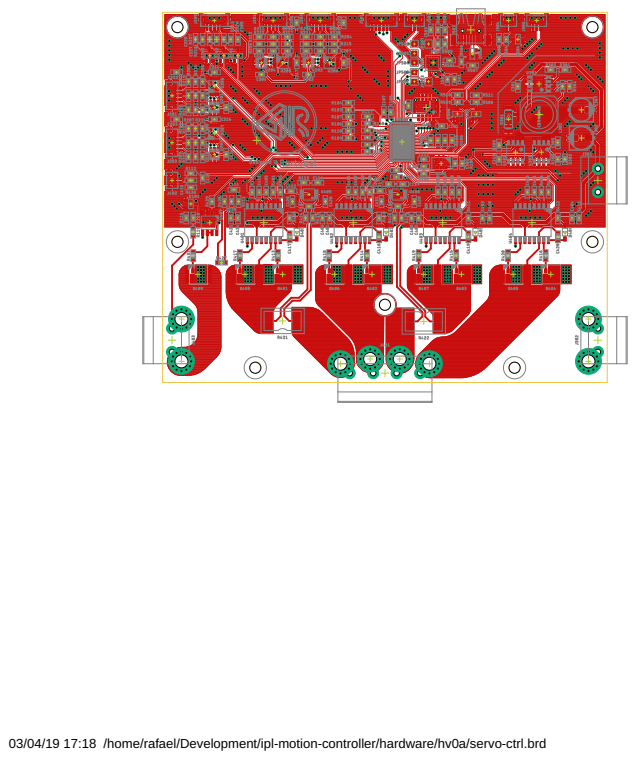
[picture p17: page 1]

03/04/19 17:18 /home/rafael/Development/ipl-motion-controller/hardware/hv0a/servo-ctrl.brd

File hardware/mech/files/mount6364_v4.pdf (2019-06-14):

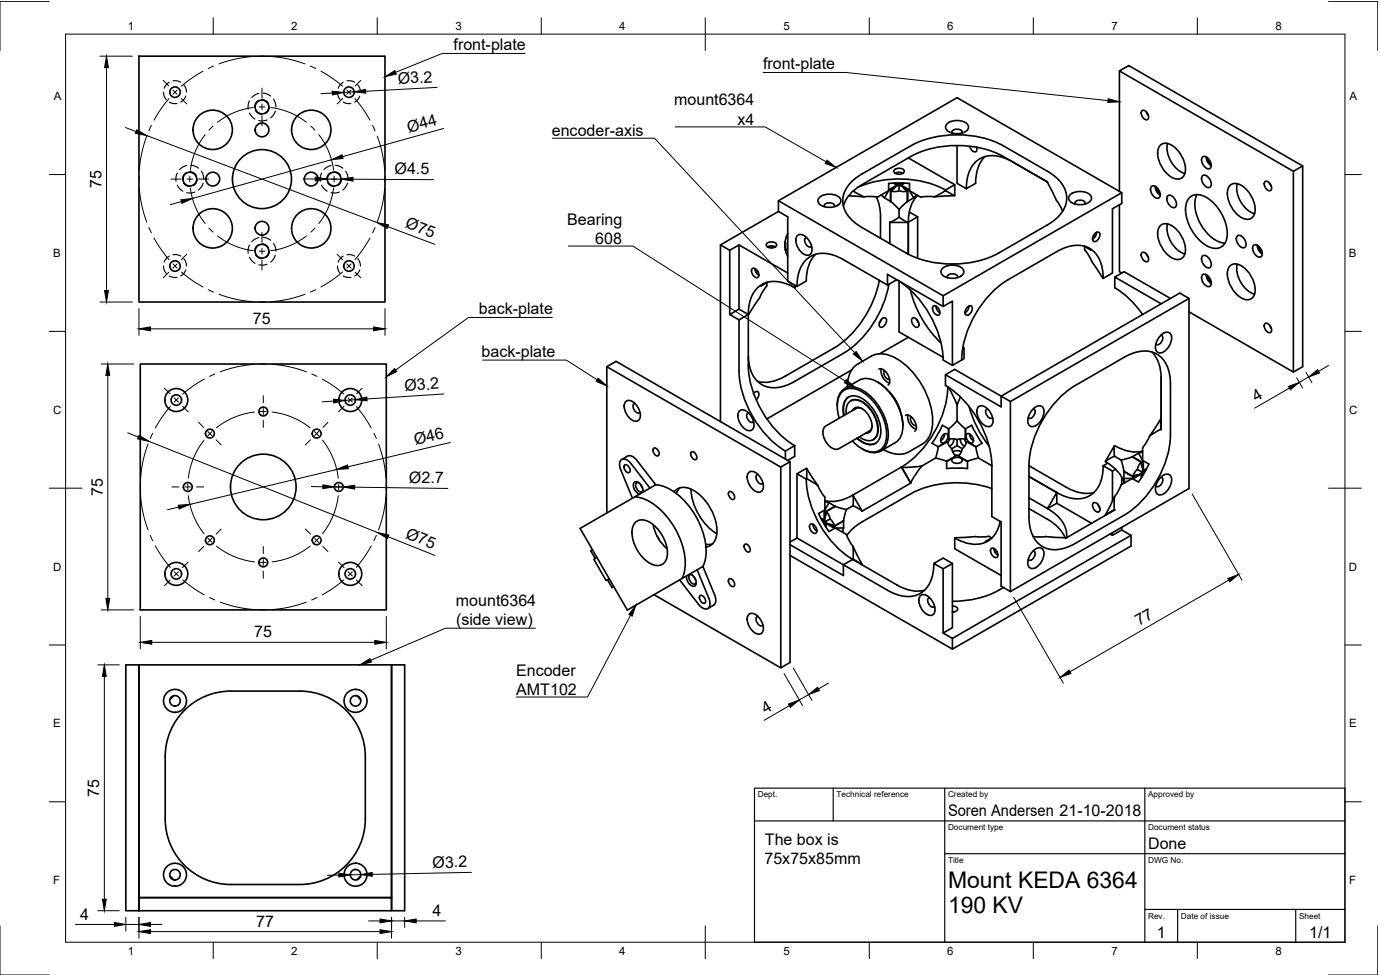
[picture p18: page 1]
(side view) 75

Dept. | Technical reference | Created by Soren Andersen 21-10-2018 | Approved by

The box is 75x75x85mm | | Document type | Document status Done

Title Mount KEDA 6364 190 KV | DWG No.

Rev. 1 | Date of issue | Sheet 1/1

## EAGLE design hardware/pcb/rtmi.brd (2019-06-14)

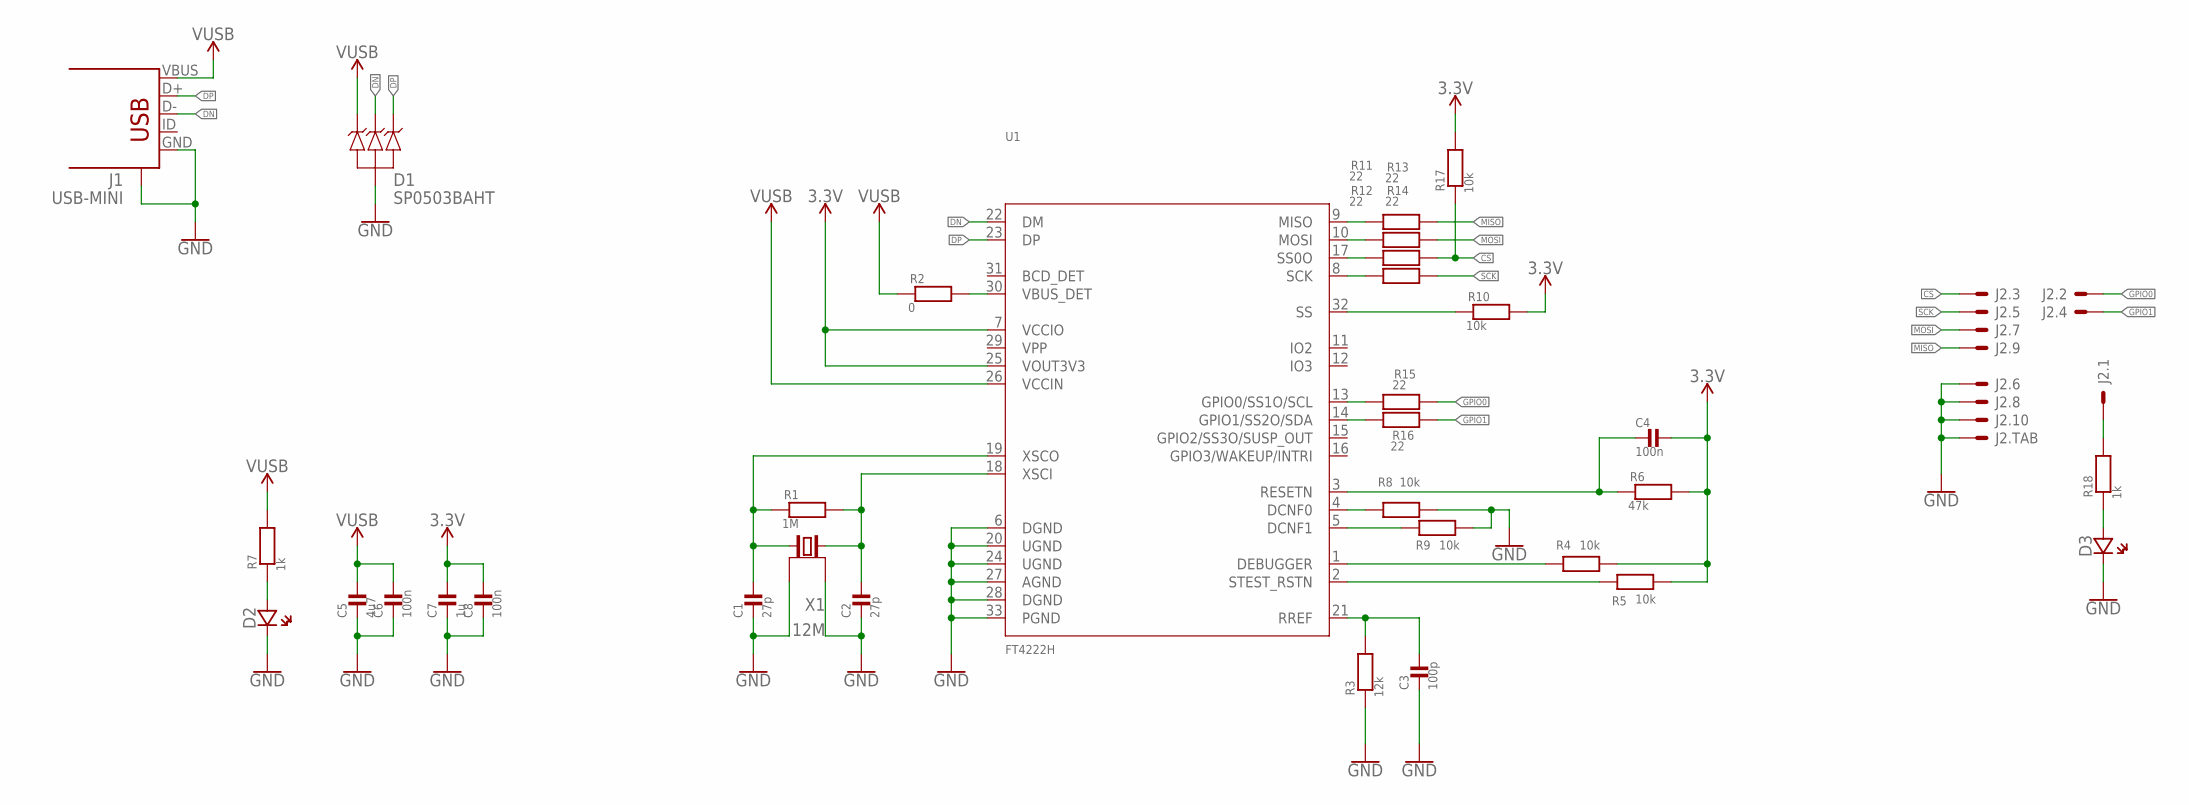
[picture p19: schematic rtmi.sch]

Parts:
C1, C2: 27p; 0603_WAVE
C3: 100p; 0603_WAVE
C4, C6, C8: 100n; 0603_WAVE
C5: 4u7; 0603_WAVE
C7: 1u; 0603_WAVE
D1: SP0503BAHT; SOT143
D2, D3: LED0603; CHIPLED_0603
J1: USB-MINI; USB-MINI-SMD
J2: F20F-10DP-1V
R1: 1M; 0603_WAVE
R2: 0; 0603_WAVE
R3: 12k; 0603_WAVE
R4, R5, R8, R9, R10, R17: 10k; 0603_WAVE
R6: 47k; 0603_WAVE
R7, R18: 1k; 0603_WAVE
R11, R12, R13, R14, R15, R16: 22; 0603_WAVE
U1: FT4222H; QFN32
X1: 12M; 4-SMD-3225

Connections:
3.3V: C4.P$1, C7.P$1, C8.P$1, R4.P$2, R5.P$2, R6.P$2, R10.P$2, R17.P$2, U1.7 (VCCIO), U1.25 (VOUT3V3)
3V3EXT: J2.1, R18.P$2
3V3EXT_LED: D3.A (AN), R18.P$1
CS: J2.3, R13.P$2, R17.P$1
DCFN1: R9.P$1, U1.5 (DCNF1)
DCNF0: R8.P$1, U1.4 (DCNF0)
DEBUGGER: R4.P$1, U1.1 (DEBUGGER)
DN: D1.3, J1.D-, U1.22 (DM)
DP: D1.4, J1.D+, U1.23 (DP)
GND: C1.P$2, C2.P$2, C3.P$2, C5.P$2, C6.P$2, C7.P$2, C8.P$2, D1.1, D2.C (CA), D3.C (CA), J1.GND, J1.GND@1 (CASE), J1.GND@2 (CASE), J1.GND@3 (CASE), J1.GND@4 (CASE), J2.6, J2.8, J2.10, J2.TAB1, J2.TAB2, R3.P$1, R8.P$2, R9.P$2, U1.6 (DGND), U1.20 (UGND), U1.24 (UGND), U1.27 (AGND), U1.28 (DGND), U1.33 (PGND), X1.2 (GND), X1.4 (GND)
GPIO0: J2.2, R15.P$2
GPIO0_PIN: R15.P$1, U1.13 (GPIO0/SS1O/SCL)
GPIO1: J2.4, R16.P$2
GPIO1_PIN: R16.P$1, U1.14 (GPIO1/SS2O/SDA)
MISO: J2.9, R11.P$2
MISO_PIN: R11.P$1, U1.9 (MISO)
MOSI: J2.7, R12.P$2
MOSI_PIN: R12.P$1, U1.10 (MOSI)
RESETN: C4.P$2, R6.P$1, U1.3 (RESETN)
RREF: C3.P$1, R3.P$2, U1.21 (RREF)
SCK: J2.5, R14.P$2
SCK_PIN: R14.P$1, U1.8 (SCK)
SS0O_PIN: R13.P$1, U1.17 (SS0O)
SS_PIN: R10.P$1, U1.32 (SS)
STEST_RSTN: R5.P$1, U1.2 (STEST_RSTN)
VBUS_DET: R2.P$2, U1.30 (VBUS_DET)
VUSB: C5.P$1, C6.P$1, D1.2, J1.VBUS, R2.P$1, R7.P$2, U1.26 (VCCIN)
VUSB_LED: D2.A (AN), R7.P$1
XSCI: C2.P$1, R1.P$2, U1.18 (XSCI), X1.1
XSCO: C1.P$1, R1.P$1, U1.19 (XSCO), X1.3 (2)

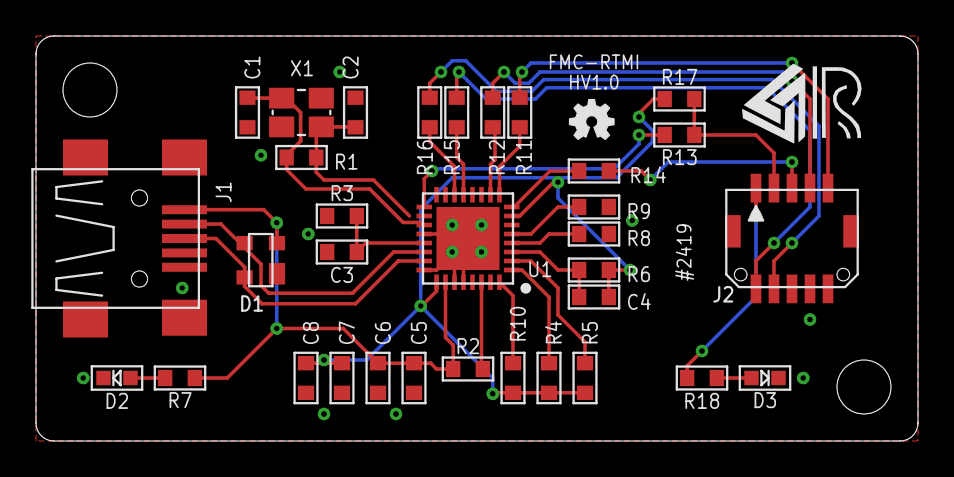
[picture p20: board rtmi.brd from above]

Board: 2 copper layers, 49.0 x 22.5 mm, 36 parts (1 on the bottom side), 30 nets.

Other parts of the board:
U$1: OSHW-LOGO-M
U$2: OSHW-LOGO-MINI
U$4: RAFAEL_SILVA_5MM_ALT_3

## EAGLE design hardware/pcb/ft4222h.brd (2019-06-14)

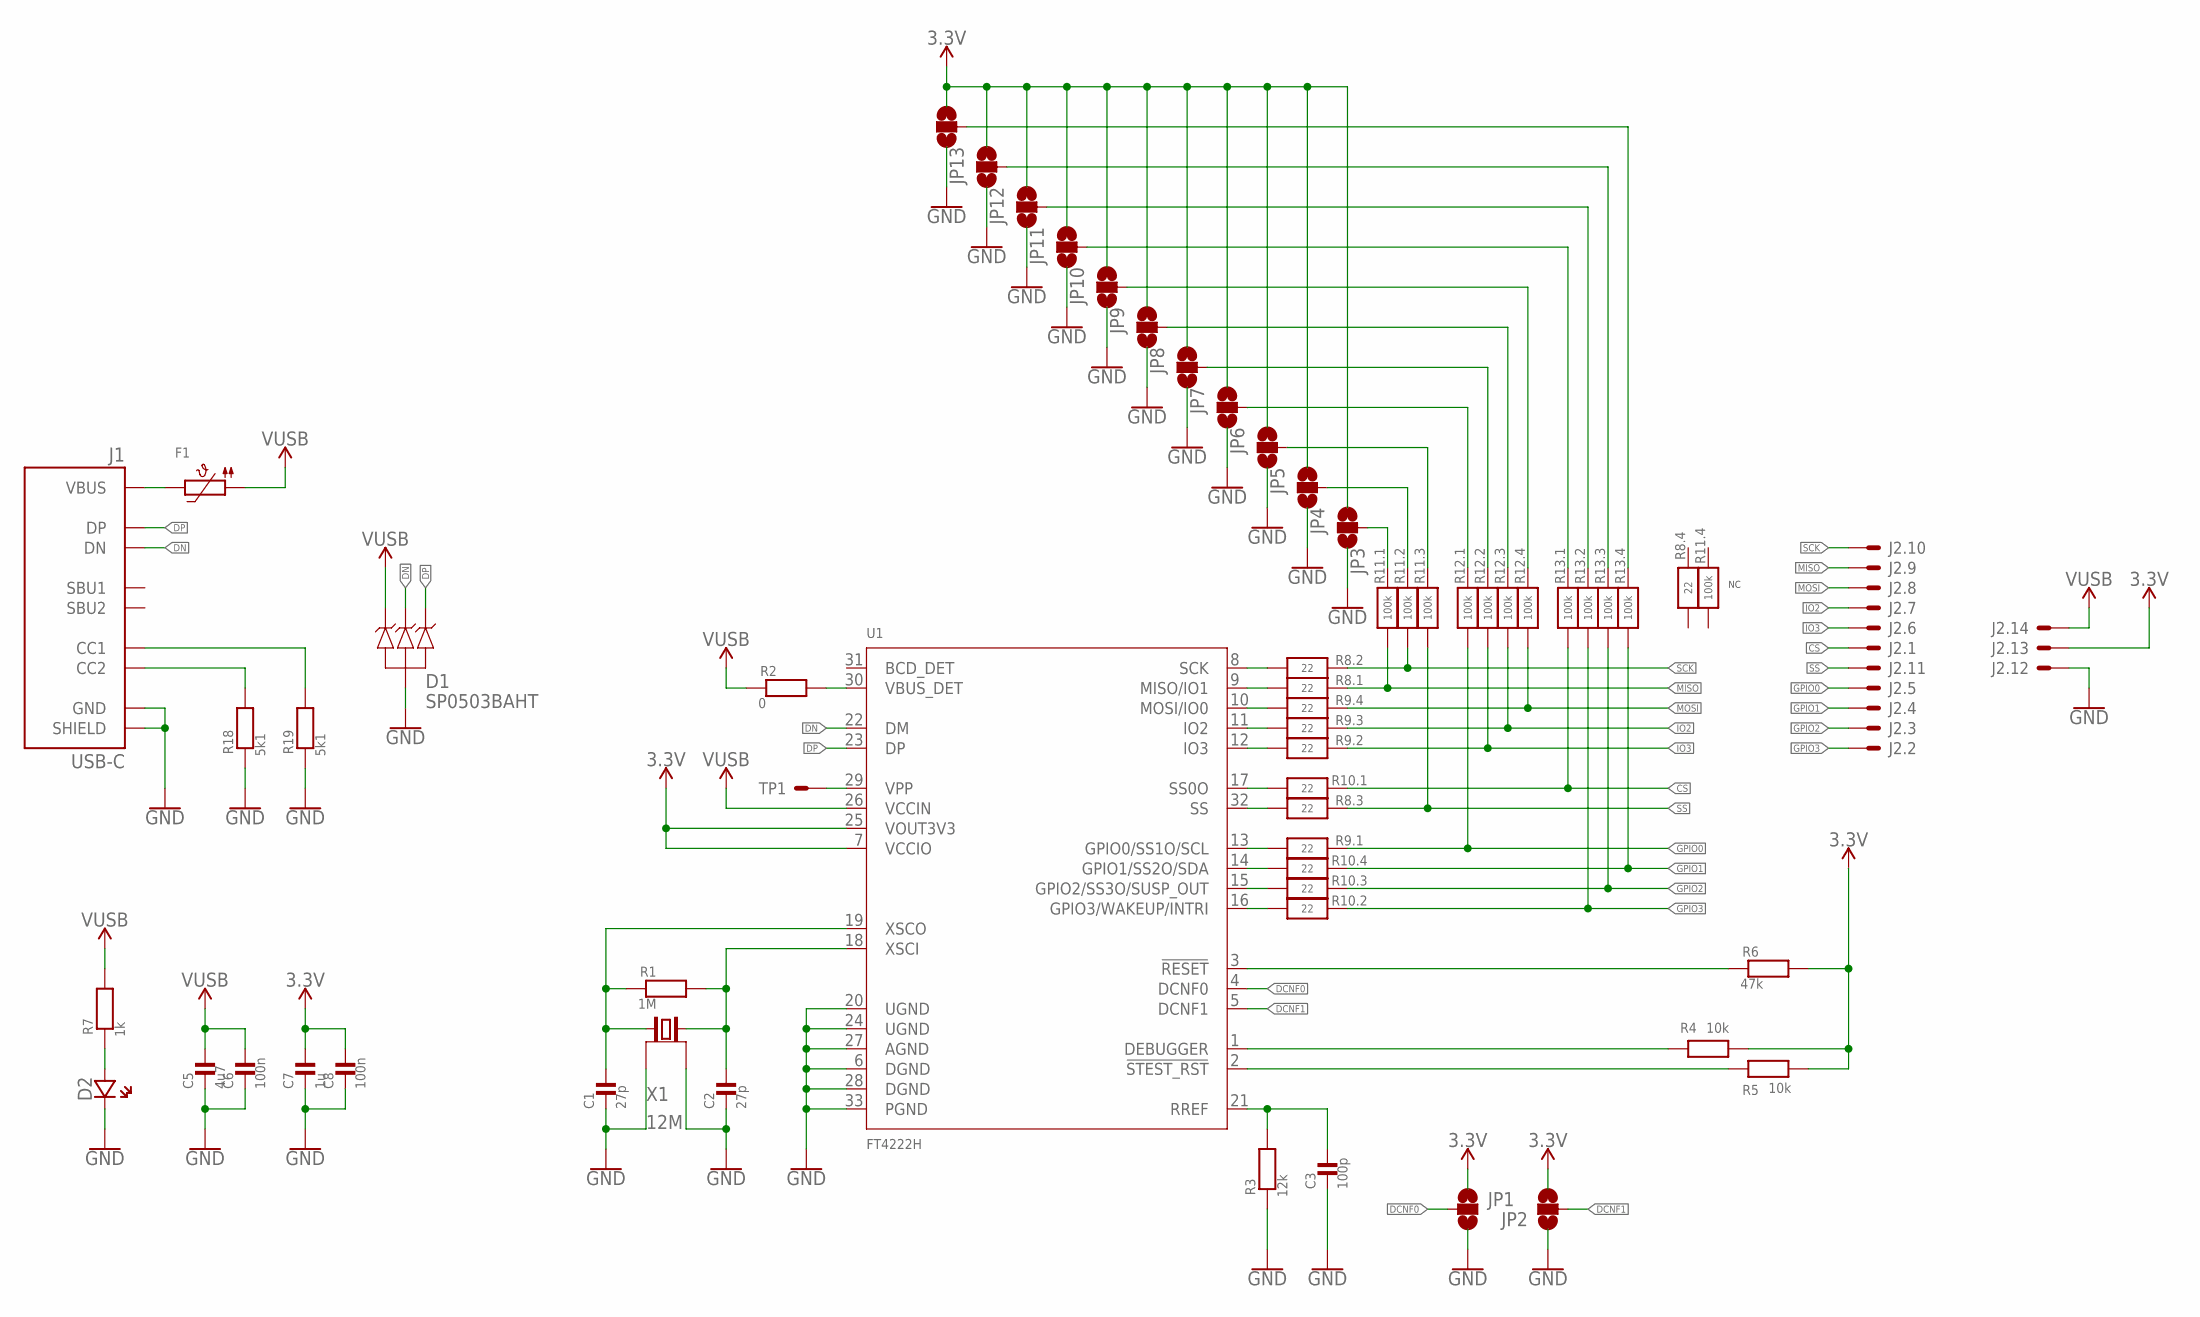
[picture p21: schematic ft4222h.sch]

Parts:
C1, C2: 27p; _0402
C3: 100p; _0402
C5: 4u7; 0603_WAVE
C6, C8: 100n; _0402
C7: 1u; 0603_WAVE
D1: SP0503BAHT; SOT143
D2: LED0603; CHIPLED_0603
F1: PTC0805; 0805
J1: USB-C
J2: 14; 2X7_2.54
JP1, JP2, JP3, JP4, JP5, JP6, JP7, JP8, JP9, JP10, JP11, JP12, JP13: JUMPER-SMT_3_NO_SILK; SMT-JUMPER_3_NO_SILK
R1: 1M; _0402
R2: 0; _0402
R3: 12k; _0402
R4, R5: 10k; _0402
R6: 47k; _0402
R7: 1k; _0402
R8, R9, R10: 22; RESPACK_4X0603
R11, R12, R13: 100k; RESPACK_4X0603
R18, R19: 5k1; _0402
TP1: TEST_POINT
U1: FT4222H; QFN32
X1: 12M; 4-SMD-3225

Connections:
3.3V: C7.P$1, C8.1, J2.13, JP1.1, JP2.3, JP3.3, JP4.3, JP5.3, JP6.3, JP7.3, JP8.3, JP9.3, JP10.3, JP11.3, JP12.3, JP13.3, R4.2, R5.2, R6.2, U1.7 (VCCIO), U1.25 (VOUT3V3)
CS: J2.1, R10.8 (2), R13.1
DCNF0: JP1.2, U1.4 (DCNF0)
DCNF1: JP2.2, U1.5 (DCNF1)
DEBUGGER: R4.1, U1.1 (DEBUGGER)
DN: D1.3, J1.A7 (DN), J1.B7 (DN), U1.22 (DM)
DP: D1.4, J1.A6 (DP), J1.B6 (DP), U1.23 (DP)
GND: C1.2, C2.2, C3.2, C5.P$2, C6.2, C7.P$2, C8.2, D1.1, D2.C (CA), J1.A1/B12 (GND), J1.B1/A12 (GND), J1.SHIELD0 (SHIELD), J1.SHIELD1 (SHIELD), J1.SHIELD2 (SHIELD), J1.SHIELD3 (SHIELD), J2.12, JP1.3, JP2.1, JP3.1, JP4.1, JP5.1, JP6.1, JP7.1, JP8.1, JP9.1, JP10.1, JP11.1, JP12.1, JP13.1, R3.1, R18.1, R19.1, U1.6 (DGND), U1.20 (UGND), U1.24 (UGND), U1.27 (AGND), U1.28 (DGND), U1.33 (PGND), X1.2 (GND), X1.4 (GND)
GPIO0: J2.5, R9.8 (2), R12.1
GPIO0_PIN: R9.1, U1.13 (GPIO0/SS1O/SCL)
GPIO0_PULL: JP6.2, R12.8 (2)
GPIO1: J2.4, R10.5 (2), R13.4 (1)
GPIO1_PIN: R10.4 (1), U1.14 (GPIO1/SS2O/SDA)
GPIO1_PULL: JP13.2, R13.5 (2)
GPIO2: J2.3, R10.6 (2), R13.3 (1)
GPIO2_PIN: R10.3 (1), U1.15 (GPIO2/SS3O/SUSP_OUT)
GPIO2_PULL: JP12.2, R13.6 (2)
GPIO3: J2.2, R10.7 (2), R13.2 (1)
GPIO3_PIN: R10.2 (1), U1.16 (GPIO3/WAKEUP/INTRI)
GPIO3_PULL: JP11.2, R13.7 (2)
IO2: J2.7, R9.6 (2), R12.3 (1)
IO2_PIN: R9.3 (1), U1.11 (IO2)
IO2_PULL: JP8.2, R12.6 (2)
IO3: J2.6, R9.7 (2), R12.2 (1)
IO3_PIN: R9.2 (1), U1.12 (IO3)
IO3_PULL: JP7.2, R12.7 (2)
MISO: J2.9, R8.8 (2), R11.1
MISO_PIN: R8.1, U1.9 (MISO/IO1)
MISO_PULL: JP3.2, R11.8 (2)
MOSI: J2.8, R9.5 (2), R12.4 (1)
MOSI_PIN: R9.4 (1), U1.10 (MOSI/IO0)
MOSI_PULL: JP9.2, R12.5 (2)
unnamed: J1.A5 (CC1), R19.2
unnamed: J1.B5 (CC2), R18.2
unnamed: F1.2, J1.A4/B9 (VBUS), J1.B4/A9 (VBUS)
unnamed: TP1.1, U1.29 (VPP)
RESETN: R6.1, U1.3 (!RESET)
RREF: C3.1, R3.2, U1.21 (RREF)
SCK: J2.10, R8.7 (2), R11.2 (1)
SCK_PIN: R8.2 (1), U1.8 (SCK)
SCK_PULL: JP4.2, R11.7 (2)
SS: J2.11, R8.6 (2), R11.3 (1)
SS0O_PIN: R10.1, U1.17 (SS0O)
SS0O_PULL: JP10.2, R13.8 (2)
SS_PIN: R8.3 (1), U1.32 (SS)
SS_PULL: JP5.2, R11.6 (2)
STEST_RSTN: R5.1, U1.2 (!STEST_RST)
VBUS_DET: R2.2, U1.30 (VBUS_DET)
VUSB: C5.P$1, C6.1, D1.2, F1.1, J2.14, R2.1, R7.2, U1.26 (VCCIN)
VUSB_LED: D2.A (AN), R7.1
XSCI: C2.1, R1.2, U1.18 (XSCI), X1.3 (2)
XSCO: C1.1, R1.1, U1.19 (XSCO), X1.1

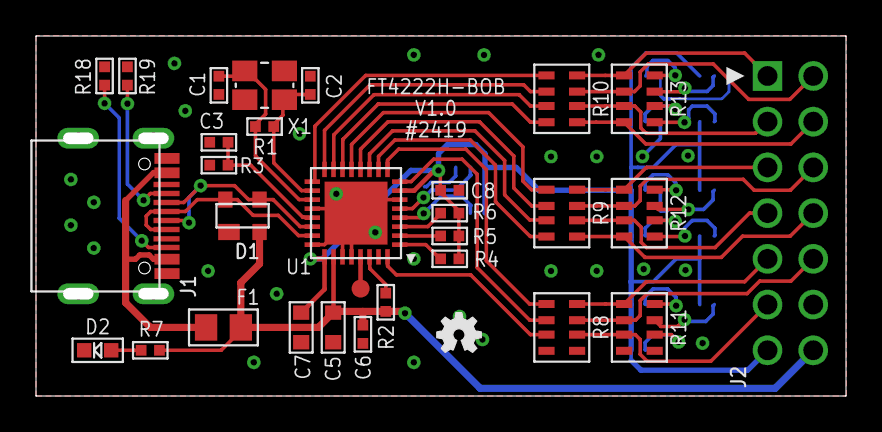
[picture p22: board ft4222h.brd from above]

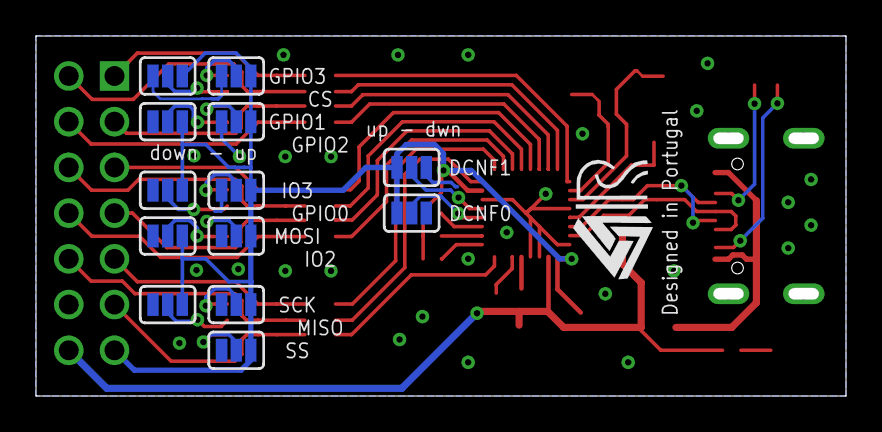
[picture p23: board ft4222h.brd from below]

Board: 2 copper layers, 45.0 x 20.0 mm, 45 parts (14 on the bottom side), 52 nets.

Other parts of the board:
U$1: OSHW-LOGO-MINI
U$2: RAFAEL_SILVA_5MM_ALT_3

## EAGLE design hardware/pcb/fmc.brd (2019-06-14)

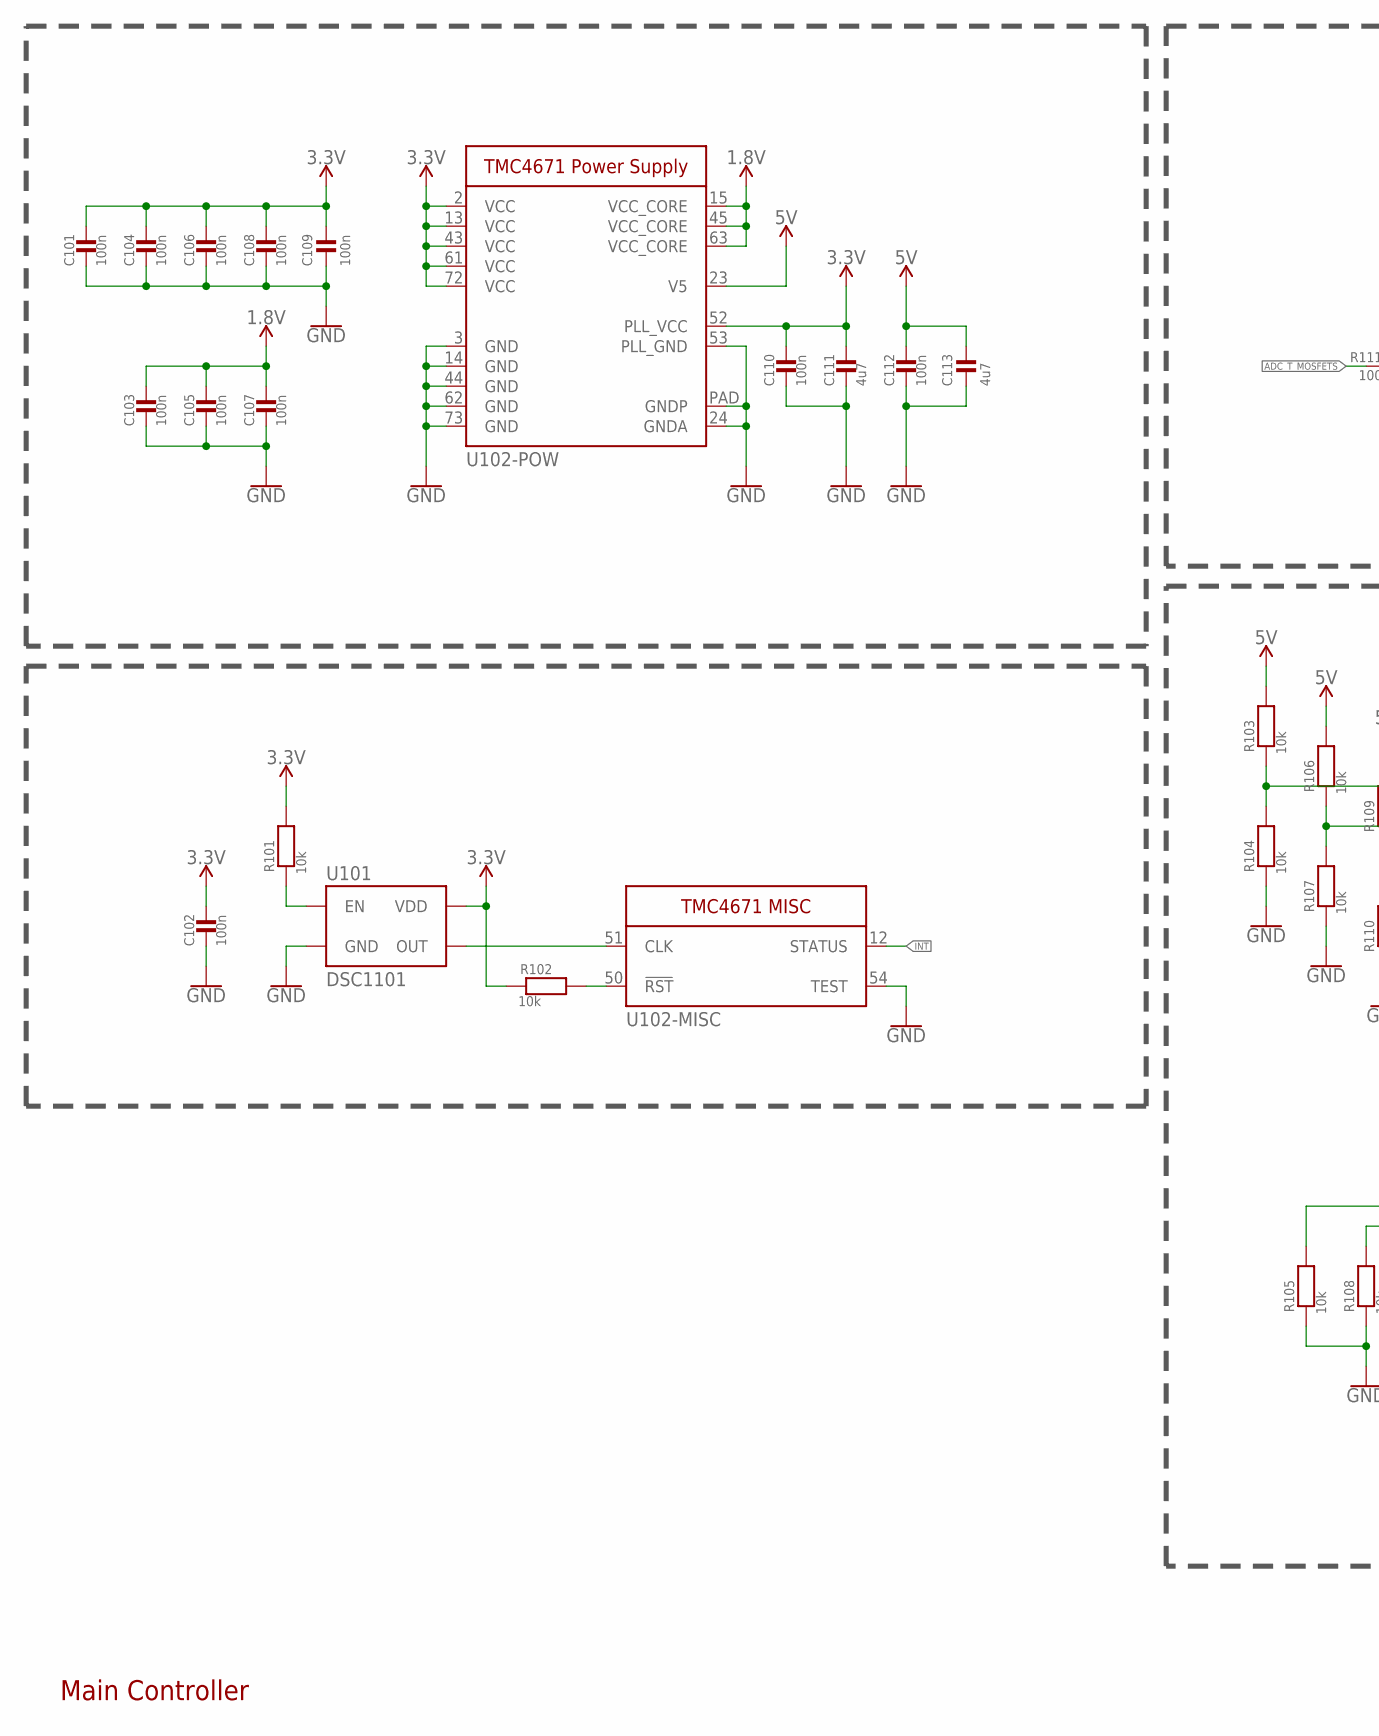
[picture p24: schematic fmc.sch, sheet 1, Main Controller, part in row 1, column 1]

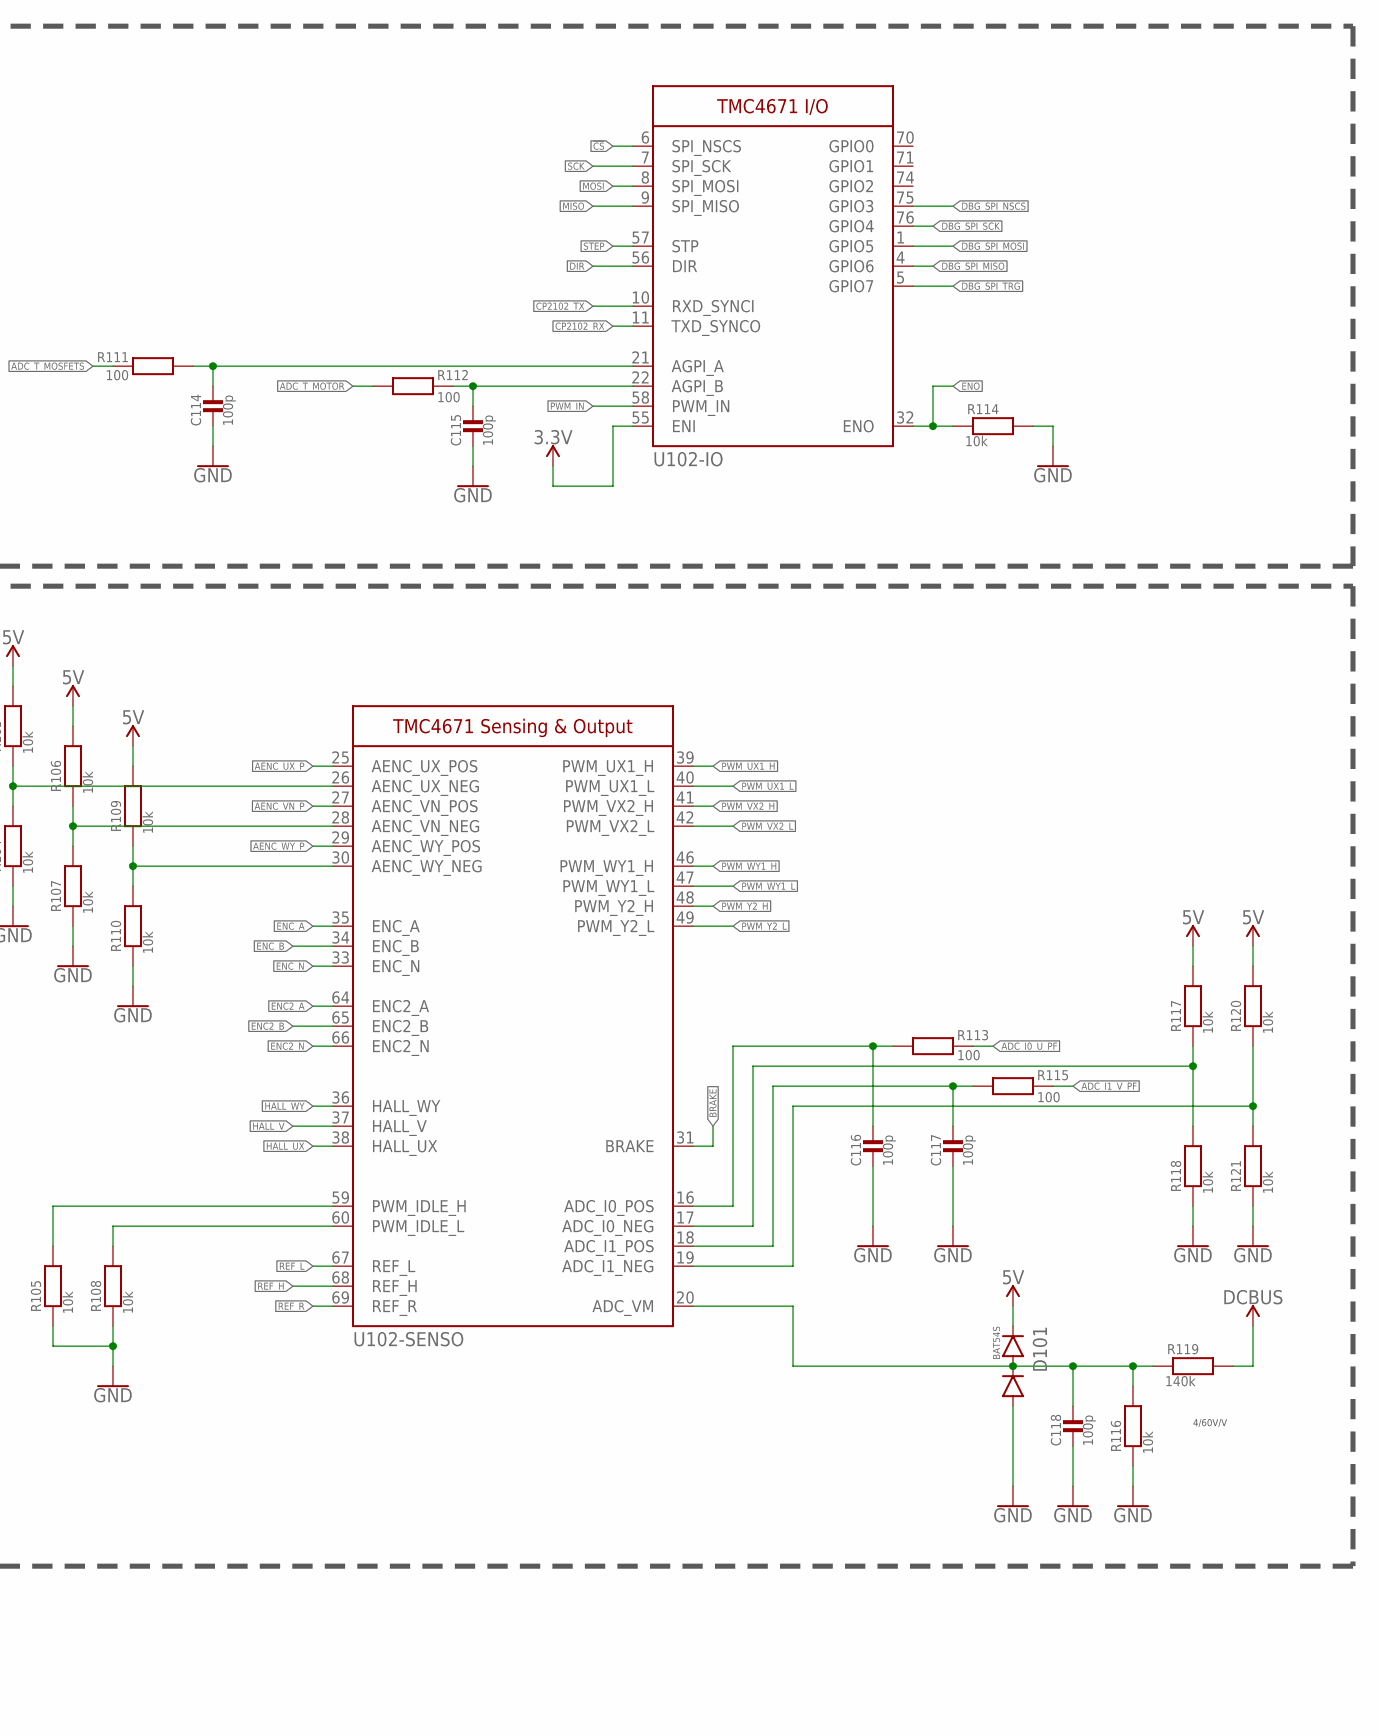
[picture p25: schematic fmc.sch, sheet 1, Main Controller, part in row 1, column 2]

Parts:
C101, C102, C103, C104, C105, C106, C107, C108, C109, C110, C112: 100n; 0603_WAVE
C111, C113: 4u7; 0603_WAVE
C114, C115, C116, C117, C118: 100p; 0603_WAVE
D101: BAT54S; SOT-23-3
R101, R102, R103, R104, R105, R106, R107, R108, R109, R110, R114, R116, R117, R118, R120, R121: 10k; 0603_WAVE
R111, R112, R113, R115: 100; 0603_WAVE
R119: 140k; 0603_WAVE
U101: DSC1101; CDFN_5X3.2
U102: TMC4671; QFN76

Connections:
1.8V: C103.P$1, C105.P$1, C107.P$1, U102.15 (VCC_CORE), U102.45 (VCC_CORE), U102.63 (VCC_CORE)
3.3V: C101.P$1, C102.P$1, C104.P$1, C106.P$1, C108.P$1, C109.P$1, C110.P$1, C111.P$1, R101.P$2, R102.P$1, U101.6 (VDD), U102.2 (VCC), U102.13 (VCC), U102.43 (VCC), U102.52 (PLL_VCC), U102.55 (ENI), U102.61 (VCC), U102.72 (VCC); also elsewhere on the board
5V: C112.P$1, C113.P$1, D101.P$2 (2), R103.P$2, R106.P$2, R109.P$2, R117.P$2, R120.P$2, U102.23 (V5); also elsewhere on the board
!CS: U102.6 (SPI_NSCS); also elsewhere on the board
ADC_I0_U_PF: R113.P$2; also elsewhere on the board
ADC_I1_V_PF: R115.P$2; also elsewhere on the board
ADC_T_MOSFETS: R111.P$2; also elsewhere on the board
ADC_T_MOTOR: R112.P$1; also elsewhere on the board
AENC_UX_P: U102.25 (AENC_UX_POS); also elsewhere on the board
AENC_VN_P: U102.27 (AENC_VN_POS); also elsewhere on the board
AENC_WY_P: U102.29 (AENC_WY_POS); also elsewhere on the board
BRAKE: U102.31 (BRAKE); also elsewhere on the board
CP2102_RX: U102.11 (TXD_SYNCO); also elsewhere on the board
CP2102_TX: U102.10 (RXD_SYNCI); also elsewhere on the board
DBG_SPI_MISO: U102.4 (GPIO6); also elsewhere on the board
DBG_SPI_MOSI: U102.1 (GPIO5); also elsewhere on the board
DBG_SPI_NSCS: U102.75 (GPIO3); also elsewhere on the board
DBG_SPI_SCK: U102.76 (GPIO4); also elsewhere on the board
DBG_SPI_TRG: U102.5 (GPIO7); also elsewhere on the board
DCBUS: R119.P$2; also elsewhere on the board
DIR: U102.56 (DIR); also elsewhere on the board
ENC2_A: U102.64 (ENC2_A); also elsewhere on the board
ENC2_B: U102.65 (ENC2_B); also elsewhere on the board
ENC2_N: U102.66 (ENC2_N); also elsewhere on the board
ENC_A: U102.35 (ENC_A); also elsewhere on the board
ENC_B: U102.34 (ENC_B); also elsewhere on the board
ENC_N: U102.33 (ENC_N); also elsewhere on the board
ENO: R114.P$1, U102.32 (ENO); also elsewhere on the board
GND: C101.P$2, C102.P$2, C103.P$2, C104.P$2, C105.P$2, C106.P$2, C107.P$2, C108.P$2, C109.P$2, C110.P$2, C111.P$2, C112.P$2, C113.P$2, C114.P$2, C115.P$2, C116.P$2, C117.P$2, C118.P$2, D101.P$1 (1), R104.P$1, R105.P$1, R107.P$1, R108.P$1, R110.P$1, R114.P$2, R116.P$1, R118.P$1, R121.P$1, U101.3 (GND), U102.3 (GND), U102.14 (GND), U102.24 (GNDA), U102.44 (GND), U102.53 (PLL_GND), U102.54 (TEST), U102.62 (GND), U102.73 (GND), U102.PAD (GNDP); also elsewhere on the board
HALL_UX: U102.38 (HALL_UX); also elsewhere on the board
HALL_V: U102.37 (HALL_V); also elsewhere on the board
HALL_WY: U102.36 (HALL_WY); also elsewhere on the board
INT: U102.12 (STATUS); also elsewhere on the board
MISO: U102.9 (SPI_MISO); also elsewhere on the board
MOSI: U102.8 (SPI_MOSI); also elsewhere on the board
unnamed: C116.P$1, R113.P$1, U102.16 (ADC_I0_POS)
unnamed: R108.P$2, U102.60 (PWM_IDLE_L)
unnamed: R105.P$2, U102.59 (PWM_IDLE_H)
unnamed: U101.4 (OUT), U102.51 (CLK)
unnamed: R102.P$2, U102.50 (!RST!)
unnamed: R101.P$1, U101.1 (EN)
unnamed: C117.P$1, R115.P$1, U102.18 (ADC_I1_POS)
unnamed: R117.P$1, R118.P$2, U102.17 (ADC_I0_NEG)
unnamed: R120.P$1, R121.P$2, U102.19 (ADC_I1_NEG)
unnamed: C118.P$1, D101.P$3 (3), R116.P$2, R119.P$1, U102.20 (ADC_VM)
unnamed: C114.P$1, R111.P$1, U102.21 (AGPI_A)
unnamed: C115.P$1, R112.P$2, U102.22 (AGPI_B)
unnamed: R109.P$1, R110.P$2, U102.30 (AENC_WY_NEG)
unnamed: R106.P$1, R107.P$2, U102.28 (AENC_VN_NEG)
unnamed: R103.P$1, R104.P$2, U102.26 (AENC_UX_NEG)
PWM_IN: U102.58 (PWM_IN); also elsewhere on the board
PWM_UX1_H: U102.39 (PWM_UX1_H); also elsewhere on the board
PWM_UX1_L: U102.40 (PWM_UX1_L); also elsewhere on the board
PWM_VX2_H: U102.41 (PWM_VX2_H); also elsewhere on the board
PWM_VX2_L: U102.42 (PWM_VX2_L); also elsewhere on the board
PWM_WY1_H: U102.46 (PWM_WY1_H); also elsewhere on the board
PWM_WY1_L: U102.47 (PWM_WY1_L); also elsewhere on the board
PWM_Y2_H: U102.48 (PWM_Y2_H); also elsewhere on the board
PWM_Y2_L: U102.49 (PWM_Y2_L); also elsewhere on the board
REF_H: U102.68 (REF_H); also elsewhere on the board
REF_L: U102.67 (REF_L); also elsewhere on the board
REF_R: U102.69 (REF_R); also elsewhere on the board
SCK: U102.7 (SPI_SCK); also elsewhere on the board
STEP: U102.57 (STP); also elsewhere on the board

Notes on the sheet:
Main Controller
4/60V/V

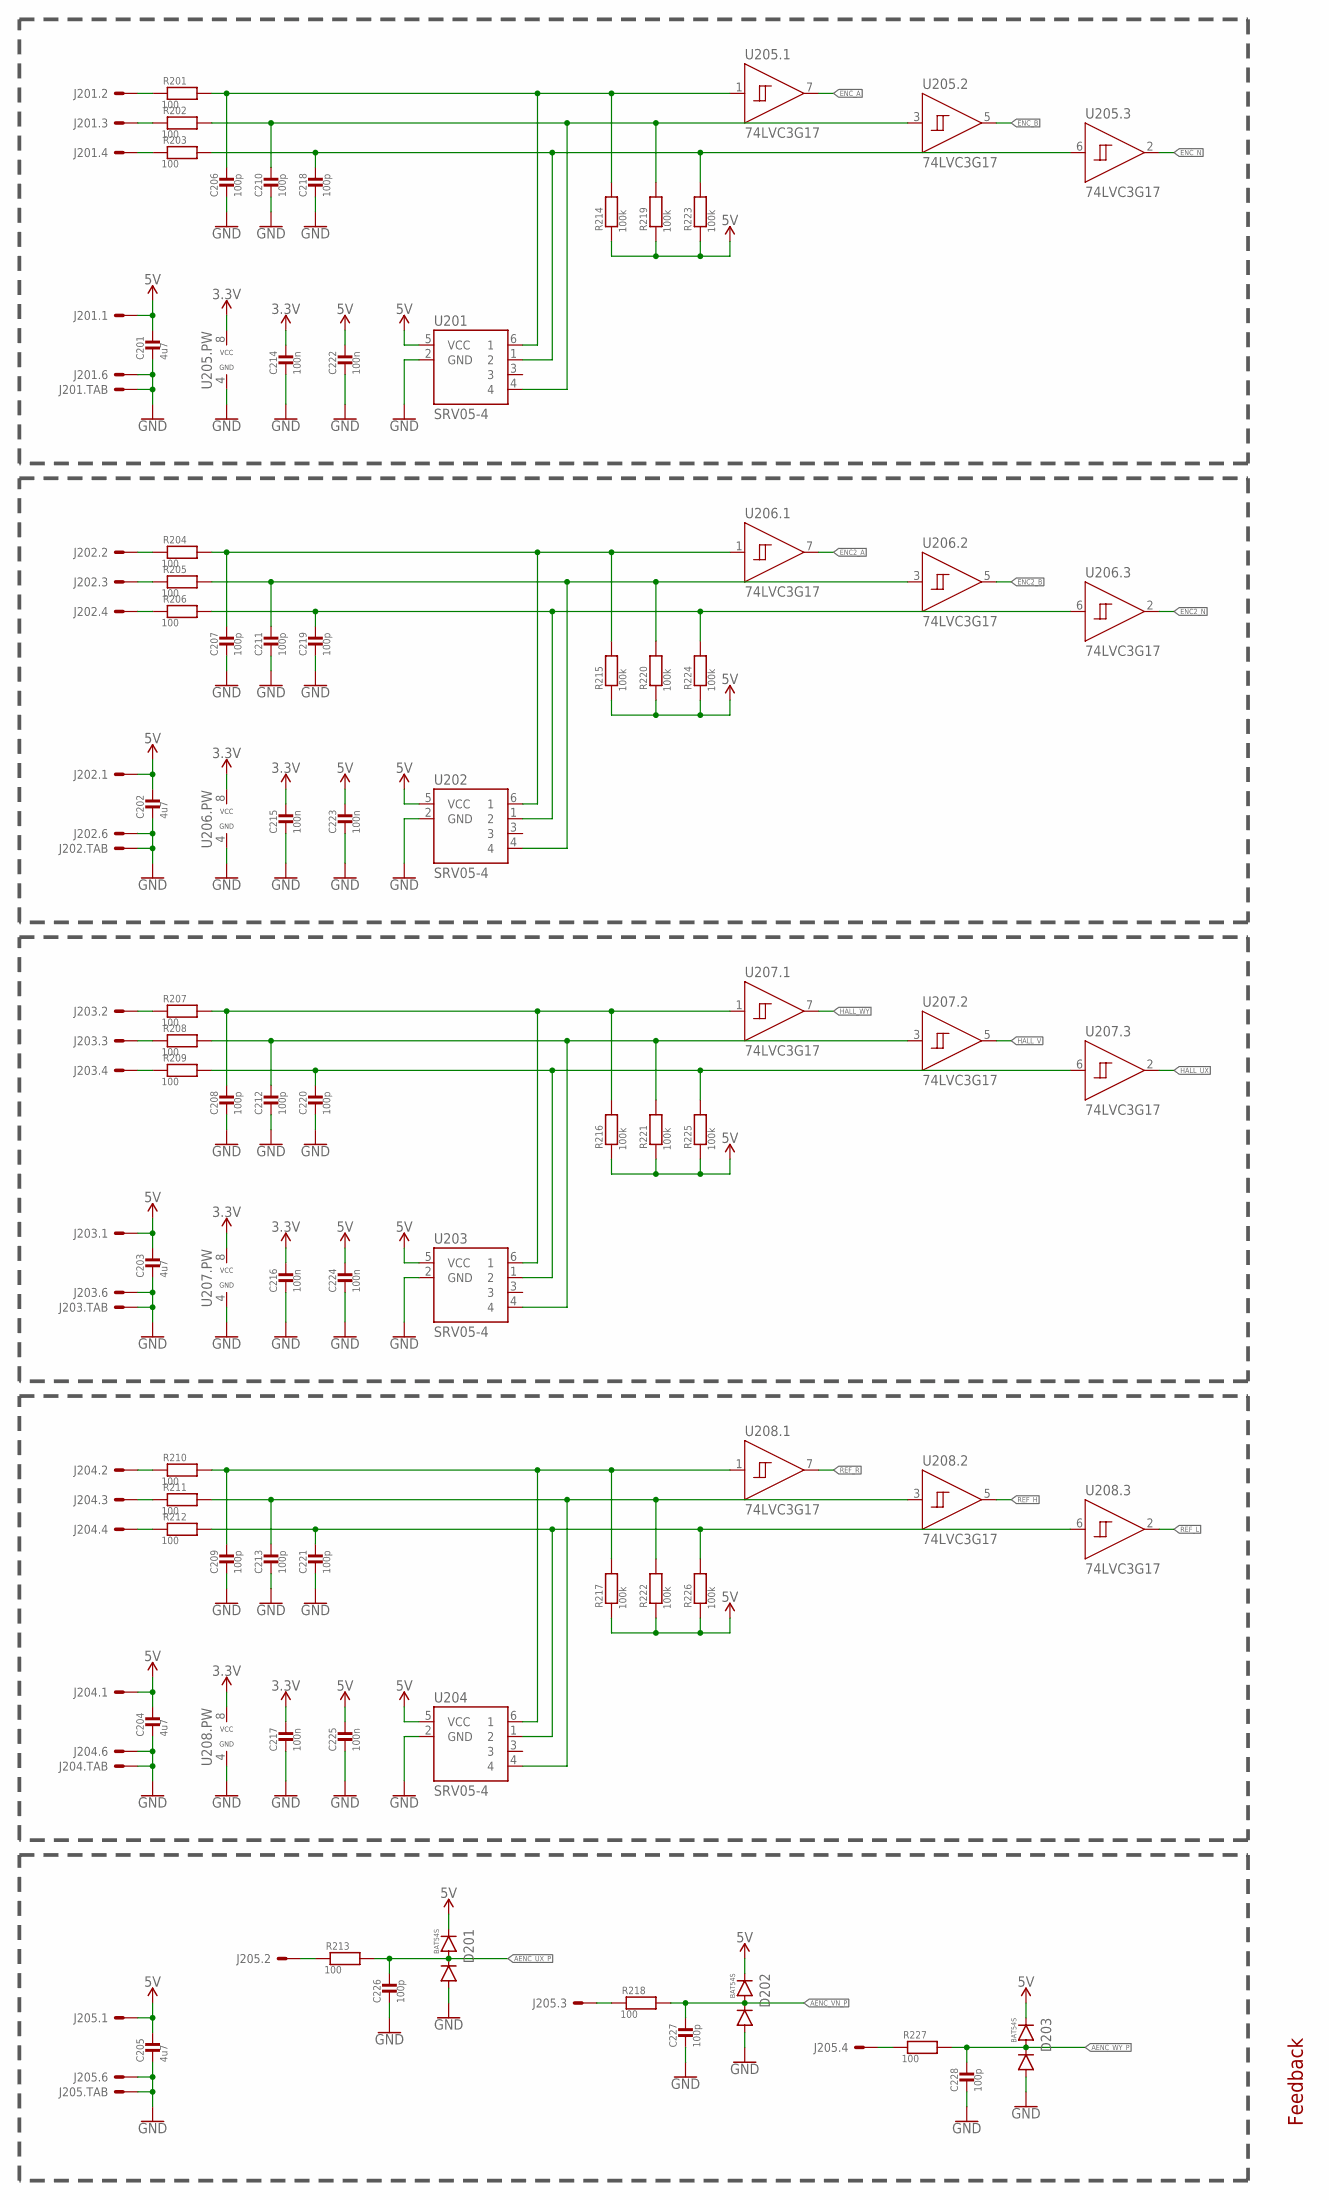
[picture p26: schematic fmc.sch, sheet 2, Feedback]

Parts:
C201, C202, C203, C204, C205: 4u7; 0603_WAVE
C206, C207, C208, C209, C210, C211, C212, C213, C218, C219, C220, C221, C226, C227, C228: 100p; 0603_WAVE
C214, C215, C216, C217, C222, C223, C224, C225: 100n; 0603_WAVE
D201, D202, D203: BAT54S; SOT-23-3
J201, J202, J203, J204, J205: SH-5; SM05B-SSR-H-TB
R201, R202, R203, R204, R205, R206, R207, R208, R209, R210, R211, R212, R213, R218, R227: 100; 0603_WAVE
R214, R215, R216, R217, R219, R220, R221, R222, R223, R224, R225, R226: 100k; 0603_WAVE
U201, U202, U203, U204: SRV05-4; SOT23-6
U205, U206, U207, U208: 74LVC3G17; TSSOP-8

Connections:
3.3V: C214.P$1, C215.P$1, C216.P$1, C217.P$1, U205.8 (VCC), U206.8 (VCC), U207.8 (VCC), U208.8 (VCC); also elsewhere on the board
5V: C201.P$1, C202.P$1, C203.P$1, C204.P$1, C205.P$1, C222.P$1, C223.P$1, C224.P$1, C225.P$1, D201.P$2 (2), D202.P$2 (2), D203.P$2 (2), J201.1, J202.1, J203.1, J204.1, J205.1, R214.P$1, R215.P$1, R216.P$1, R217.P$1, R219.P$1, R220.P$1, R221.P$1, R222.P$1, R223.P$1, R224.P$1, R225.P$1, R226.P$1, U201.5 (VCC), U202.5 (VCC), U203.5 (VCC), U204.5 (VCC); also elsewhere on the board
AENC_UX@J: J205.2, R213.P$1
AENC_UX_P: C226.P$1, D201.P$3 (3), R213.P$2; also elsewhere on the board
AENC_VN@J: J205.3, R218.P$1
AENC_VN_P: C227.P$1, D202.P$3 (3), R218.P$2; also elsewhere on the board
AENC_WY@J: J205.4, R227.P$1
AENC_WY_P: C228.P$1, D203.P$3 (3), R227.P$2; also elsewhere on the board
ENC2_A: U206.7 (Y); also elsewhere on the board
ENC2_B: U206.5 (Y); also elsewhere on the board
ENC2_N: U206.2 (Y); also elsewhere on the board
ENC_2_A@J: J202.2, R204.P$1
ENC_2_B@J: J202.3, R205.P$1
ENC_2_N@J: J202.4, R206.P$1
ENC_A: U205.7 (Y); also elsewhere on the board
ENC_A@J: J201.2, R201.P$1
ENC_B: U205.5 (Y); also elsewhere on the board
ENC_B@J: J201.3, R202.P$1
ENC_N: U205.2 (Y); also elsewhere on the board
ENC_N@J: J201.4, R203.P$1
GND: C201.P$2, C202.P$2, C203.P$2, C204.P$2, C205.P$2, C206.P$2, C207.P$2, C208.P$2, C209.P$2, C210.P$2, C211.P$2, C212.P$2, C213.P$2, C214.P$2, C215.P$2, C216.P$2, C217.P$2, C218.P$2, C219.P$2, C220.P$2, C221.P$2, C222.P$2, C223.P$2, C224.P$2, C225.P$2, C226.P$2, C227.P$2, C228.P$2, D201.P$1 (1), D202.P$1 (1), D203.P$1 (1), J201.5, J201.FIT@1, J201.FIT@2, J202.5, J202.FIT@1, J202.FIT@2, J203.5, J203.FIT@1, J203.FIT@2, J204.5, J204.FIT@1, J204.FIT@2, J205.5, J205.FIT@1, J205.FIT@2, U201.2 (GND), U202.2 (GND), U203.2 (GND), U204.2 (GND), U205.4 (GND), U206.4 (GND), U207.4 (GND), U208.4 (GND); also elsewhere on the board
HALL_UX: U207.2 (Y); also elsewhere on the board
HALL_UX@J: J203.4, R209.P$1
HALL_V: U207.5 (Y); also elsewhere on the board
HALL_V@J: J203.3, R208.P$1
HALL_WY: U207.7 (Y); also elsewhere on the board
HALL_WY@J: J203.2, R207.P$1
unnamed: C218.P$1, R203.P$2, R223.P$2, U201.1 (2), U205.6 (A)
unnamed: C210.P$1, R202.P$2, R219.P$2, U201.4, U205.3 (A)
unnamed: C219.P$1, R206.P$2, R224.P$2, U202.1 (2), U206.6 (A)
unnamed: C206.P$1, R201.P$2, R214.P$2, U201.6 (1), U205.1 (A)
unnamed: C211.P$1, R205.P$2, R220.P$2, U202.4, U206.3 (A)
unnamed: C207.P$1, R204.P$2, R215.P$2, U202.6 (1), U206.1 (A)
unnamed: C220.P$1, R209.P$2, R225.P$2, U203.1 (2), U207.6 (A)
unnamed: C212.P$1, R208.P$2, R221.P$2, U203.4, U207.3 (A)
unnamed: C208.P$1, R207.P$2, R216.P$2, U203.6 (1), U207.1 (A)
unnamed: C221.P$1, R212.P$2, R226.P$2, U204.1 (2), U208.6 (A)
unnamed: C213.P$1, R211.P$2, R222.P$2, U204.4, U208.3 (A)
unnamed: C209.P$1, R210.P$2, R217.P$2, U204.6 (1), U208.1 (A)
REF_H: U208.5 (Y); also elsewhere on the board
REF_H@J: J204.3, R211.P$1
REF_L: U208.2 (Y); also elsewhere on the board
REF_L@J: J204.4, R212.P$1
REF_R: U208.7 (Y); also elsewhere on the board
REF_R@J: J204.2, R210.P$1

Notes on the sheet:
Feedback

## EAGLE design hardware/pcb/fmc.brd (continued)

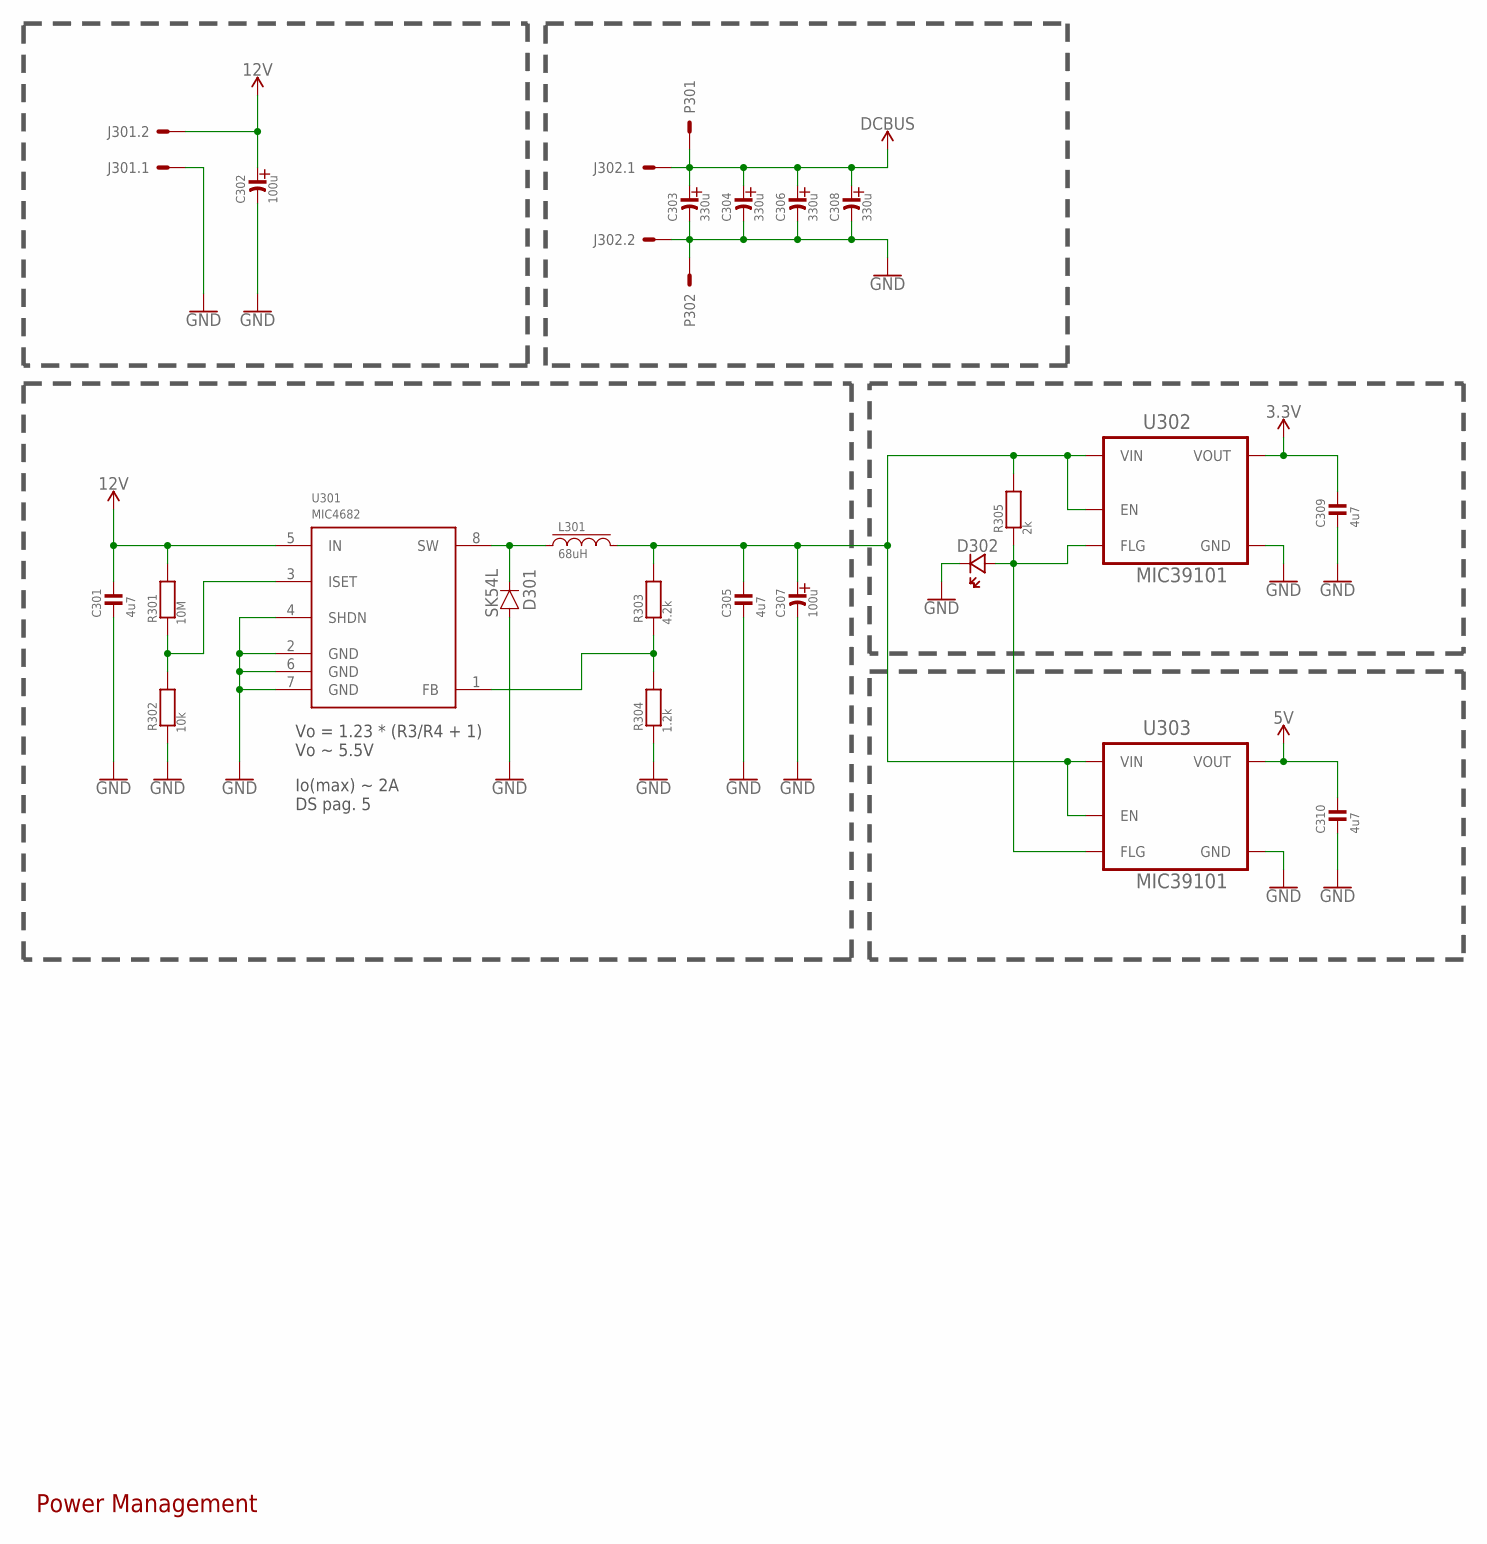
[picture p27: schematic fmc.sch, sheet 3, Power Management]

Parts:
C301, C305, C309, C310: 4u7; 0603_WAVE
C302, C307: 100u; PANASONIC_D
C303, C304, C306, C308: 330u; PANASONIC_G
D301: SK54L; DO214AA
D302: LED0603; CHIPLED_0603
J301, J302: 2P-6.35P
L301: 68uH; CDRH104R
P301, P302: POWPAD; TH-HP
R301: 10M; 0603_WAVE
R302: 10k; 0603_WAVE
R303: 4.2k; 0603_WAVE
R304: 1.2k; 0603_WAVE
R305: 2k; 0603_WAVE
U301: MIC4682; SOIC8
U302, U303: MIC39101; SOIC8

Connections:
3.3V: C309.P$1, U302.3 (VOUT); also elsewhere on the board
5V: C310.P$1, U303.3 (VOUT); also elsewhere on the board
12V: C301.P$1, C302.+ (AN), J301.2, R301.P$2, U301.5 (IN); also elsewhere on the board
DCBUS: C303.+ (AN), C304.+ (AN), C306.+ (AN), C308.+ (AN), J302.1, P301.H1, P301.H2, P301.H3, P301.H4, P301.H5, P301.H6, P301.H7, P301.H8, P301.H9, P301.H10, P301.H11, P301.H12, P301.PAD; also elsewhere on the board
GND: C301.P$2, C302.- (CA), C303.- (CA), C304.- (CA), C305.P$2, C306.- (CA), C307.- (CA), C308.- (CA), C309.P$2, C310.P$2, D301.A, D302.C (CA), J301.1, J302.2, P302.H1, P302.H2, P302.H3, P302.H4, P302.H5, P302.H6, P302.H7, P302.H8, P302.H9, P302.H10, P302.H11, P302.H12, P302.PAD, R302.P$1, R304.P$1, U301.2 (GND), U301.4 (SHDN), U301.6 (GND), U301.7 (GND), U302.5 (GND), U302.6 (GND), U302.7 (GND), U302.8 (GND), U303.5 (GND), U303.6 (GND), U303.7 (GND), U303.8 (GND); also elsewhere on the board
unnamed: C305.P$1, C307.+ (AN), L301.2, R303.P$2, R305.P$2, U302.1 (EN), U302.2 (VIN), U303.1 (EN), U303.2 (VIN)
unnamed: D301.C, L301.1, U301.8 (SW)
unnamed: R303.P$1, R304.P$2, U301.1 (FB)
unnamed: R301.P$1, R302.P$2, U301.3 (ISET)
unnamed: D302.A (AN), R305.P$1, U302.4 (FLG), U303.4 (FLG)

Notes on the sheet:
Power Management
Vo = 1.23 * (R3/R4 + 1) Vo ~ 5.5V
Io(max) ~ 2A DS pag. 5

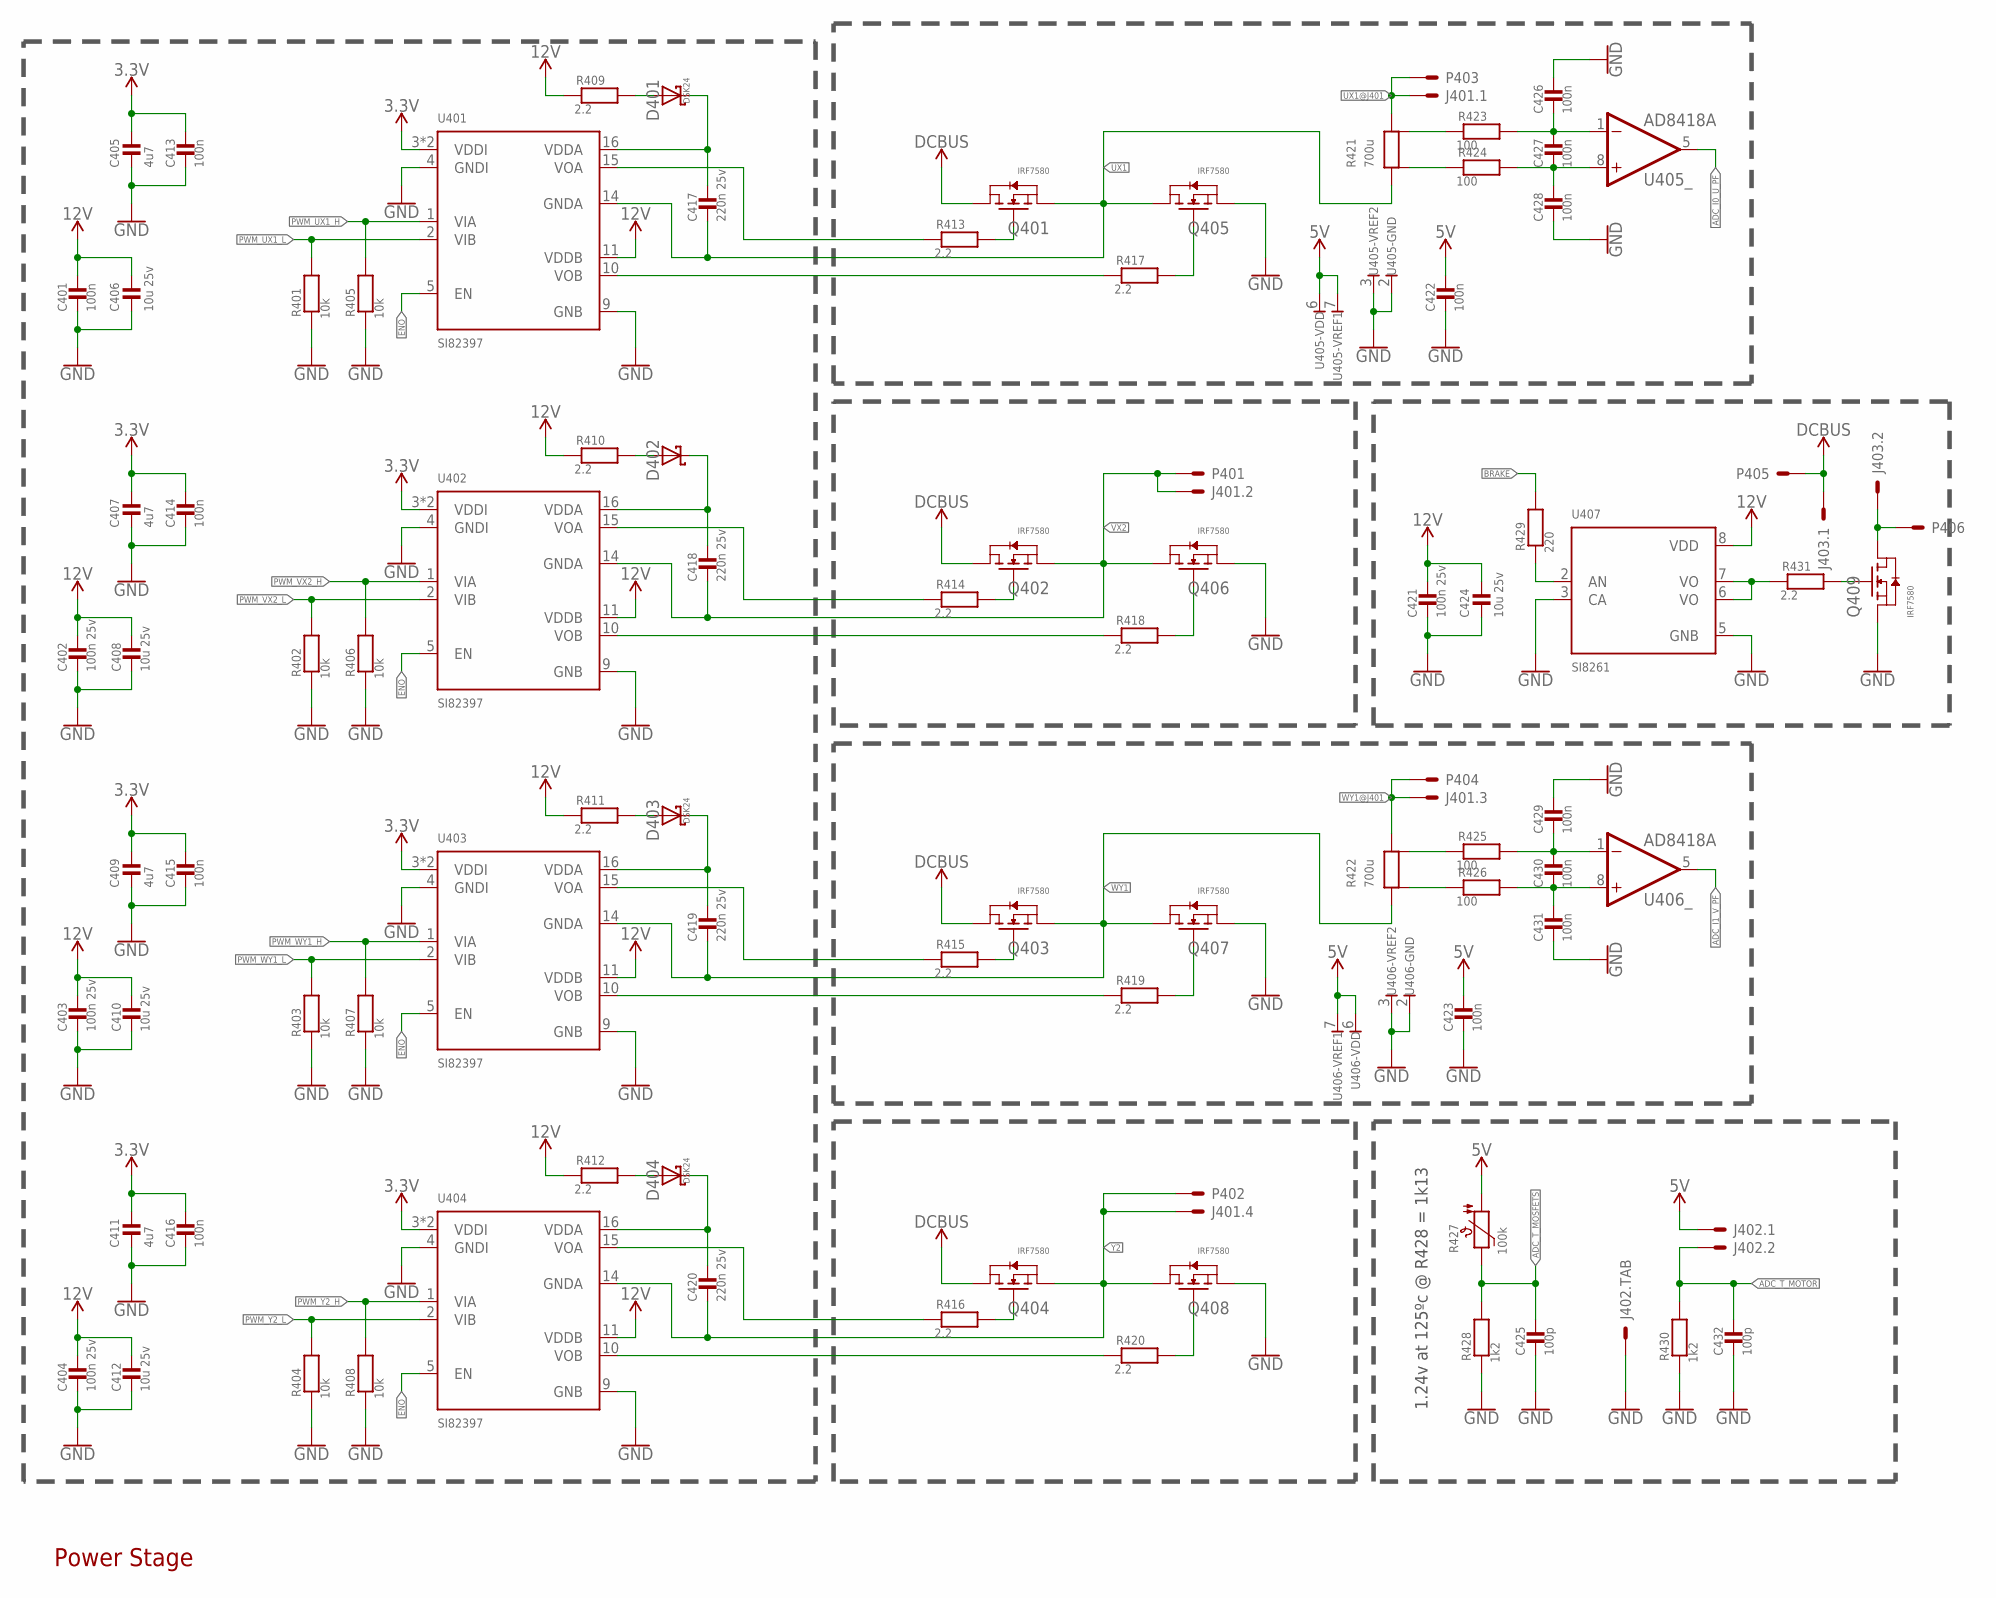
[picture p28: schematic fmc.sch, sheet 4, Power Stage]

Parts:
C401, C413, C414, C415, C416, C422, C423, C426, C427, C428, C429, C430, C431: 100n; 0603_WAVE
C402, C403, C404, C421: 100n 25v; 0603_WAVE
C405, C407, C409, C411: 4u7; 0603_WAVE
C406, C408, C410, C412, C424: 10u 25v; 0603_WAVE
C417, C418, C419, C420: 220n 25v; 0603_WAVE
C425, C432: 100p; 0603_WAVE
D401, D402, D403, D404: DSK24; SOD-123
J401: 4P-6.35P
J402: SH-2; SM02B-SSR-H-TB
J403: 2P-6.35P
P401, P402, P403, P404, P405, P406: POWPAD; TH-HP
Q401, Q402, Q403, Q404, Q405, Q406, Q407, Q408, Q409: IRF7580; DIRECTFET-ME
R401, R402, R403, R404, R405, R406, R407, R408: 10k; 0603_WAVE
R409, R410, R411, R412, R413, R414, R415, R416, R417, R418, R419, R420, R431: 2.2; 0603_WAVE
R421, R422: 700u; 3920
R423, R424, R425, R426: 100; 0603_WAVE
R427: 100k; 0603_WAVE
R428, R430: 1k2; 0603_WAVE
R429: 220; 0603_WAVE
U401, U402, U403, U404: SI82397; SOIC-16-WB
U405, U406: AD8418A; MSOP-8
U407: SI8261; SOIC_8

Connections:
3.3V: C405.P$1, C407.P$1, C409.P$1, C411.P$1, C413.P$1, C414.P$1, C415.P$1, C416.P$1, U401.3 (VDDI), U401.8 (VDDI), U402.3 (VDDI), U402.8 (VDDI), U403.3 (VDDI), U403.8 (VDDI), U404.3 (VDDI), U404.8 (VDDI); also elsewhere on the board
5V: C422.P$1, C423.P$1, J402.1, R427.P$2, U405.6, U405.7, U406.6, U406.7; also elsewhere on the board
12V: C401.P$1, C402.P$1, C403.P$1, C404.P$1, C406.P$1, C408.P$1, C410.P$1, C412.P$1, C421.P$1, C424.P$1, R409.P$1, R410.P$1, R411.P$1, R412.P$1, U401.11 (VDDB), U402.11 (VDDB), U403.11 (VDDB), U404.11 (VDDB), U407.8 (VDD); also elsewhere on the board
ADC_I0_U_PF: U405.5 (O); also elsewhere on the board
ADC_I1_V_PF: U406.5 (O); also elsewhere on the board
ADC_T_MOSFETS: C425.P$1, R427.P$1, R428.P$2; also elsewhere on the board
ADC_T_MOTOR: C432.P$1, J402.2, R430.P$2; also elsewhere on the board
BRAKE: R429.P$2; also elsewhere on the board
DCBUS: J403.1, P405.H1, P405.H2, P405.H3, P405.H4, P405.H5, P405.H6, P405.H7, P405.H8, P405.H9, P405.H10, P405.H11, P405.H12, P405.PAD, Q401.D1, Q401.D2 (D1), Q401.D3 (D1), Q401.D4 (D1), Q402.D1, Q402.D2 (D1), Q402.D3 (D1), Q402.D4 (D1), Q403.D1, Q403.D2 (D1), Q403.D3 (D1), Q403.D4 (D1), Q404.D1, Q404.D2 (D1), Q404.D3 (D1), Q404.D4 (D1); also elsewhere on the board
ENO: U401.5 (EN), U402.5 (EN), U403.5 (EN), U404.5 (EN); also elsewhere on the board
GND: C401.P$2, C402.P$2, C403.P$2, C404.P$2, C405.P$2, C406.P$2, C407.P$2, C408.P$2, C409.P$2, C410.P$2, C411.P$2, C412.P$2, C413.P$2, C414.P$2, C415.P$2, C416.P$2, C421.P$2, C422.P$2, C423.P$2, C424.P$2, C425.P$2, C426.P$1, C428.P$2, C429.P$1, C431.P$2, C432.P$2, J402.FIT@1, J402.FIT@2, Q405.S1, Q405.S2 (S1), Q405.S3 (S1), Q405.S4 (S1), Q405.S5 (S1), Q406.S1, Q406.S2 (S1), Q406.S3 (S1), Q406.S4 (S1), Q406.S5 (S1), Q407.S1, Q407.S2 (S1), Q407.S3 (S1), Q407.S4 (S1), Q407.S5 (S1), Q408.S1, Q408.S2 (S1), Q408.S3 (S1), Q408.S4 (S1), Q408.S5 (S1), Q409.S1, Q409.S2 (S1), Q409.S3 (S1), Q409.S4 (S1), Q409.S5 (S1), R401.P$1, R402.P$1, R403.P$1, R404.P$1, R405.P$1, R406.P$1, R407.P$1, R408.P$1, R428.P$1, R430.P$1, U401.4 (GNDI), U401.9 (GNB), U402.4 (GNDI), U402.9 (GNB), U403.4 (GNDI), U403.9 (GNB), U404.4 (GNDI), U404.9 (GNB), U405.2, U405.3, U406.2, U406.3, U407.3 (CA), U407.5 (GNB); also elsewhere on the board
unnamed: R413.P$1, U401.15 (VOA)
unnamed: Q405.G (G1), R417.P$2
unnamed: R421.SENSE+, R424.P$1
unnamed: C417.P$1, D401.C, U401.16 (VDDA)
unnamed: R414.P$1, U402.15 (VOA)
unnamed: Q406.G (G1), R418.P$2
unnamed: R421.SENSE-, R423.P$1
unnamed: C418.P$1, D402.C, U402.16 (VDDA)
unnamed: R415.P$1, U403.15 (VOA)
unnamed: Q407.G (G1), R419.P$2
unnamed: C426.P$2, C427.P$1, R423.P$2, U405.1 (IN-)
unnamed: C419.P$1, D403.C, U403.16 (VDDA)
unnamed: R416.P$1, U404.15 (VOA)
unnamed: Q408.G (G1), R420.P$2
unnamed: C427.P$2, C428.P$1, R424.P$2, U405.8 (IN+)
unnamed: C420.P$1, D404.C, U404.16 (VDDA)
unnamed: Q403.G (G1), R415.P$2
unnamed: Q401.G (G1), R413.P$2
unnamed: Q402.G (G1), R414.P$2
unnamed: Q404.G (G1), R416.P$2
unnamed: R417.P$1, U401.10 (VOB)
unnamed: R418.P$1, U402.10 (VOB)
unnamed: R419.P$1, U403.10 (VOB)
unnamed: R420.P$1, U404.10 (VOB)
unnamed: D404.A, R412.P$2
unnamed: D403.A, R411.P$2
unnamed: D402.A, R410.P$2
unnamed: D401.A, R409.P$2
unnamed: R422.SENSE-, R425.P$1
unnamed: R422.SENSE+, R426.P$1
unnamed: C430.P$2, C431.P$1, R426.P$2, U406.8 (IN+)
unnamed: C429.P$2, C430.P$1, R425.P$2, U406.1 (IN-)
unnamed: R429.P$1, U407.2 (AN)
unnamed: Q409.G (G1), R431.P$2
unnamed: R431.P$1, U407.6 (VO), U407.7 (VO)
unnamed: J403.2, P406.H1, P406.H2, P406.H3, P406.H4, P406.H5, P406.H6, P406.H7, P406.H8, P406.H9, P406.H10, P406.H11, P406.H12, P406.PAD, Q409.D1, Q409.D2 (D1), Q409.D3 (D1), Q409.D4 (D1)
PWM_UX1_H: R405.P$2, U401.1 (VIA); also elsewhere on the board
PWM_UX1_L: R401.P$2, U401.2 (VIB); also elsewhere on the board
PWM_VX2_H: R406.P$2, U402.1 (VIA); also elsewhere on the board
PWM_VX2_L: R402.P$2, U402.2 (VIB); also elsewhere on the board
PWM_WY1_H: R407.P$2, U403.1 (VIA); also elsewhere on the board
PWM_WY1_L: R403.P$2, U403.2 (VIB); also elsewhere on the board
PWM_Y2_H: R408.P$2, U404.1 (VIA); also elsewhere on the board
PWM_Y2_L: R404.P$2, U404.2 (VIB); also elsewhere on the board
UX1: C417.P$2, Q401.S1, Q401.S2 (S1), Q401.S3 (S1), Q401.S4 (S1), Q401.S5 (S1), Q405.D1, Q405.D2 (D1), Q405.D3 (D1), Q405.D4 (D1), R421.1, R421.2, U401.14 (GNDA)
UX1@J401: J401.1, P403.H1, P403.H2, P403.H3, P403.H4, P403.H5, P403.H6, P403.H7, P403.H8, P403.H9, P403.H10, P403.H11, P403.H12, P403.PAD, R421.3, R421.4
VX2: C418.P$2, J401.2, P401.H1, P401.H2, P401.H3, P401.H4, P401.H5, P401.H6, P401.H7, P401.H8, P401.H9, P401.H10, P401.H11, P401.H12, P401.PAD, Q402.S1, Q402.S2 (S1), Q402.S3 (S1), Q402.S4 (S1), Q402.S5 (S1), Q406.D1, Q406.D2 (D1), Q406.D3 (D1), Q406.D4 (D1), U402.14 (GNDA)
WY1: C419.P$2, Q403.S1, Q403.S2 (S1), Q403.S3 (S1), Q403.S4 (S1), Q403.S5 (S1), Q407.D1, Q407.D2 (D1), Q407.D3 (D1), Q407.D4 (D1), R422.1, R422.2, U403.14 (GNDA)
WY1@J401: J401.3, P404.H1, P404.H2, P404.H3, P404.H4, P404.H5, P404.H6, P404.H7, P404.H8, P404.H9, P404.H10, P404.H11, P404.H12, P404.PAD, R422.3, R422.4
Y2: C420.P$2, J401.4, P402.H1, P402.H2, P402.H3, P402.H4, P402.H5, P402.H6, P402.H7, P402.H8, P402.H9, P402.H10, P402.H11, P402.H12, P402.PAD, Q404.S1, Q404.S2 (S1), Q404.S3 (S1), Q404.S4 (S1), Q404.S5 (S1), Q408.D1, Q408.D2 (D1), Q408.D3 (D1), Q408.D4 (D1), U404.14 (GNDA)

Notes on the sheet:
Power Stage
1.24v at 125ºc @ R428 = 1k13

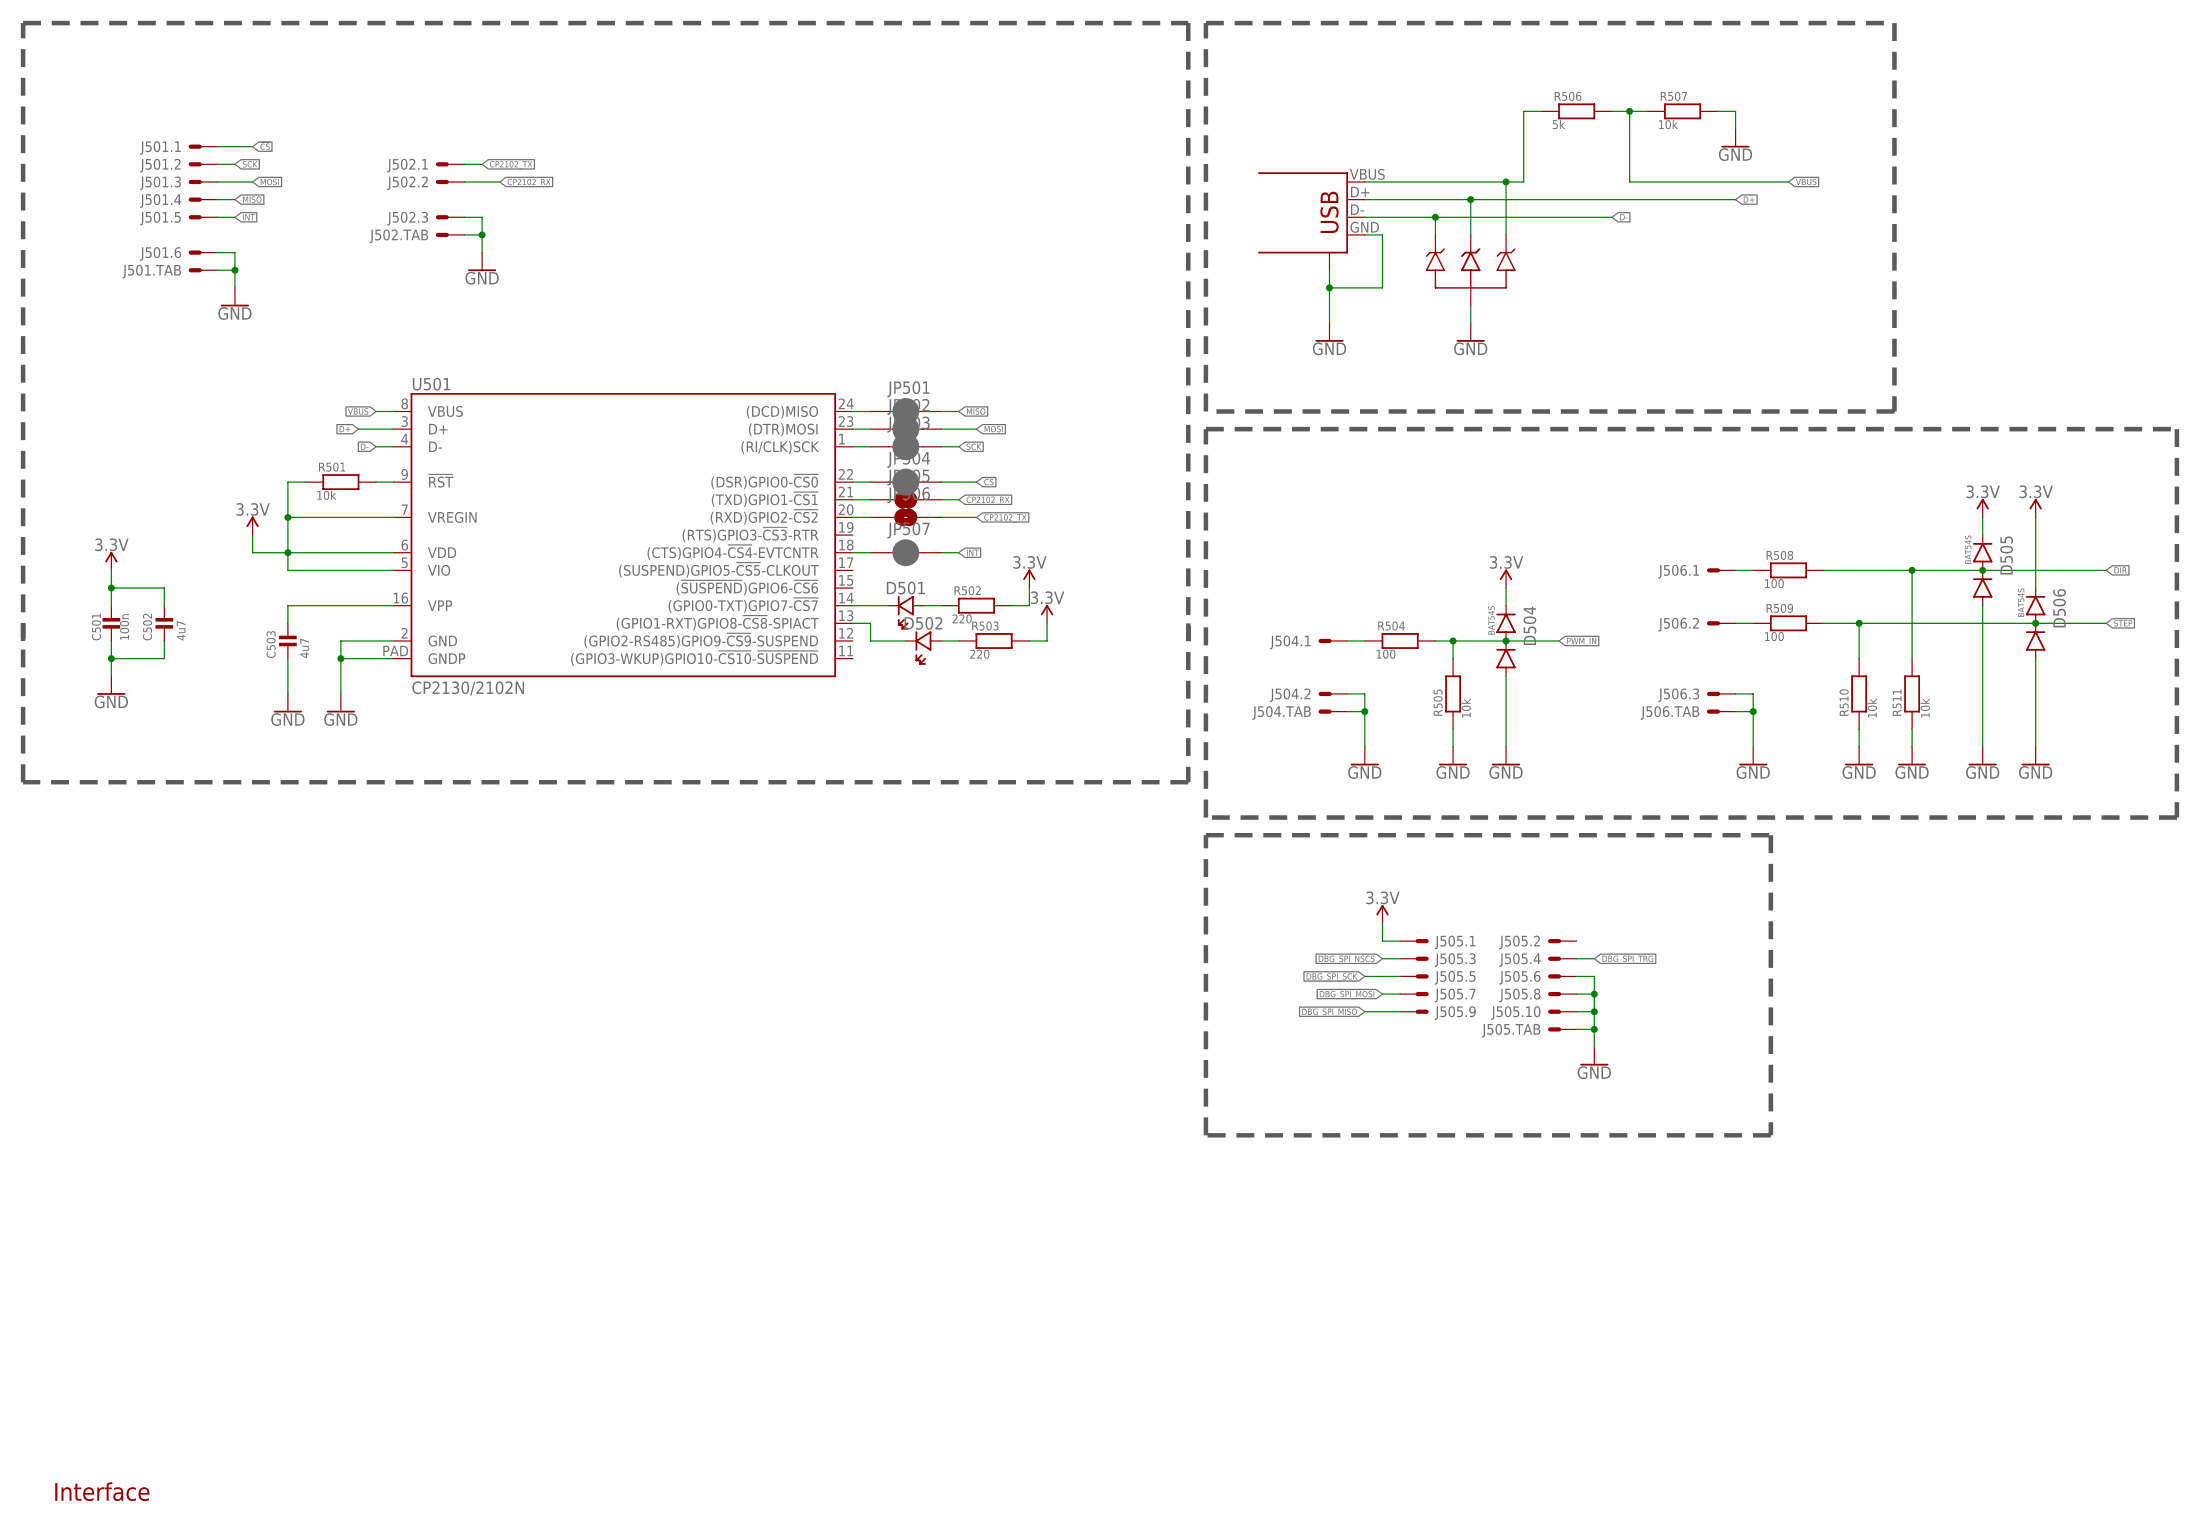
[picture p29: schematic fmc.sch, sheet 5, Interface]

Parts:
C501: 100n; 0603_WAVE
C502, C503: 4u7; 0603_WAVE
D501, D502: LED0603; CHIPLED_0603
D503: SP0503BAHT; SOT143
D504, D505, D506: BAT54S; SOT-23-3
J501: SH-6; SM06B-SSR-H-TB
J502, J506: SH-3; SM03B-SSR-H-TB
J503: USB-SHIELD; USB-M-S1
J504: SH-2; SM02B-SSR-H-TB
J505: F20F-10DP-1V
JP501, JP502, JP503, JP504, JP507: JUMPER-SMT_2_NC_PASTE_SILK; SMT-JUMPER_2_NC_PASTE_SILK
JP505, JP506: JUMPER-SMT_2_NO_SILK; SMT-JUMPER_2_NO_SILK
R501, R505, R507, R510, R511: 10k; 0603_WAVE
R502, R503: 220; 0603_WAVE
R504, R508, R509: 100; 0603_WAVE
R506: 5k; 0603_WAVE
U501: CP2130/2102N; QFN24

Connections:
3.3V: C501.P$1, C502.P$1, D504.P$2 (2), D505.P$2 (2), D506.P$2 (2), J505.1, R501.P$1, R502.P$2, R503.P$2, U501.5 (VIO), U501.6 (VDD), U501.7 (VREGIN); also elsewhere on the board
!CS: J501.1, JP504.2; also elsewhere on the board
CP2102_RX: J502.2, JP505.2; also elsewhere on the board
CP2102_TX: J502.1, JP506.2; also elsewhere on the board
D+: D503.3, J503.D+, U501.3 (D+)
D-: D503.2, J503.D-, U501.4 (D-)
DBG_SPI_MISO: J505.9; also elsewhere on the board
DBG_SPI_MOSI: J505.7; also elsewhere on the board
DBG_SPI_NSCS: J505.3; also elsewhere on the board
DBG_SPI_SCK: J505.5; also elsewhere on the board
DBG_SPI_TRG: J505.4; also elsewhere on the board
DIR: D505.P$3 (3), R508.P$2, R511.P$2; also elsewhere on the board
DIR@J: J506.1, R508.P$1
GND: C501.P$2, C502.P$2, C503.P$2, D503.1, D504.P$1 (1), D505.P$1 (1), D506.P$1 (1), J501.6, J501.FIT@1, J501.FIT@2, J502.3, J502.FIT@1, J502.FIT@2, J503.GND, J503.GND@1 (CASE), J503.GND@2 (CASE), J503.GND@3 (CASE), J503.GND@4 (CASE), J504.2, J504.FIT@1, J504.FIT@2, J505.6, J505.8, J505.10, J505.TAB1, J505.TAB2, J506.3, J506.FIT@1, J506.FIT@2, R505.P$1, R507.P$2, R510.P$1, R511.P$1, U501.2 (GND), U501.PAD (GNDP); also elsewhere on the board
INT: J501.5, JP507.2; also elsewhere on the board
MISO: J501.4, JP501.2; also elsewhere on the board
MOSI: J501.3, JP502.2; also elsewhere on the board
unnamed: D503.4, J503.VBUS, R506.P$1
unnamed: R501.P$2, U501.9 (!RST)
unnamed: C503.P$1, U501.16 (VPP)
unnamed: D501.C (CA), U501.14 ((GPIO0-TXT)GPIO7-!CS7)
unnamed: D502.C (CA), U501.13 ((GPIO1-RXT)GPIO8-!CS8!-SPIACT)
unnamed: D501.A (AN), R502.P$1
unnamed: D502.A (AN), R503.P$1
unnamed: JP506.1, U501.20 ((RXD)GPIO2-!CS2)
unnamed: JP505.1, U501.21 ((TXD)GPIO1-!CS1)
unnamed: JP507.1, U501.18 ((CTS)GPIO4-!CS4!-EVTCNTR)
unnamed: JP504.1, U501.22 ((DSR)GPIO0-!CS0)
unnamed: JP503.1, U501.1 ((RI/CLK)SCK)
unnamed: JP502.1, U501.23 ((DTR)MOSI)
unnamed: JP501.1, U501.24 ((DCD)MISO)
PWM_IN: D504.P$3 (3), R504.P$2, R505.P$2; also elsewhere on the board
PWM_IN@J: J504.1, R504.P$1
SCK: J501.2, JP503.2; also elsewhere on the board
STEP: D506.P$3 (3), R509.P$2, R510.P$2; also elsewhere on the board
STEP@J: J506.2, R509.P$1
VBUS: R506.P$2, R507.P$1, U501.8 (VBUS)

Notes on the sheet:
Interface

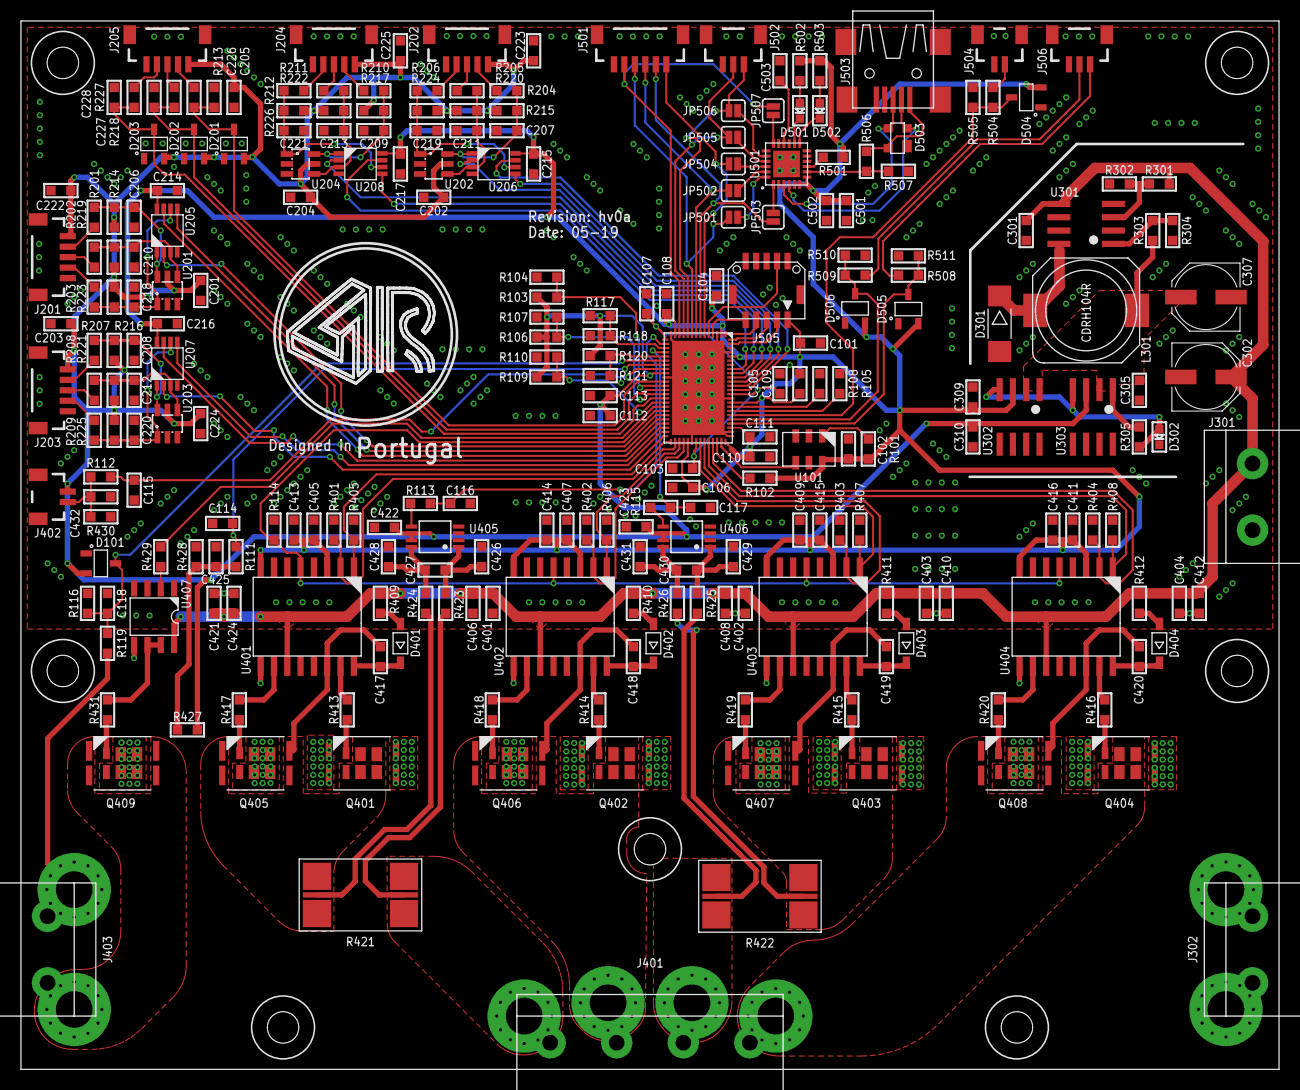
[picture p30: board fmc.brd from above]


Board: 2 copper layers, 120.0 x 100.0 mm, 265 parts (4 on the bottom side), 159 nets.

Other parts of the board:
U$1: RAFAEL_SILVA_10MM_CIRCLE

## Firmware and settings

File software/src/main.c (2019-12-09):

#include <libusb-1.0/libusb.h>
#include <stdlib.h>
#include <stdio.h>

#include <signal.h>

#include "utils.h"
#include "debug_macros.h"
#include "cp2130.h"
#include "tmc4671.h"

static volatile sig_atomic_t gxKeepRunning = 1;

void sig_handler(int signo);

int main(void)
{
    setvbuf(stdout, NULL, _IONBF, 0);
    setvbuf(stderr, NULL, _IONBF, 0);

    signal(SIGINT, sig_handler);

    libusb_context *ctx = NULL;
    if(libusb_init(&ctx) < 0)
    {
		printf("error: failed in libusb init\n\r");
        return EXIT_FAILURE;
	}

    cp2130_device_t *spi = cp2130_init(ctx, CP2130_DEFAULT_VID, CP2130_DEFAULT_PID);

    if(!spi)
    {
        printf("error: failed to initialize device\n\r");
        return EXIT_FAILURE;
    }

    uint8_t ubMajor, ubMinor;
    cp2130_get_version(spi, &ubMajor, &ubMinor);
    printf("Version: %0d.%0d\n\r", ubMajor, ubMinor);

    cp2130_set_usb_cfg(spi, 0x10C4, 0x87A0, CP2130_USP_MAX_POW_MA(500u), CP2130_USB_BUS_POW_REG_EN, 3, 0, CP2130_USB_PRIORITY_WRITE, CP2130_USB_CFG_MSK_MAX_POW);

    uint16_t usVid, usPid;
    uint8_t ubMaxPow, ubPowMode, ubTransferPriority;
    cp2130_get_usb_cfg(spi, &usVid, &usPid, &ubMaxPow, &ubPowMode, &ubMajor, &ubMinor, &ubTransferPriority);
    printf("VID: 0x%04X\n\r", usVid);
    printf("PID: 0x%04X\n\r", usPid);
    printf("Max Power: %dma\n\r", ubMaxPow * 2);
    printf("Power Mode: 0x%02X\n\r", ubPowMode);
    printf("Transfer Priority: 0x%02X\n\r", ubTransferPriority);

    uint8_t ubStr[63];
    memset(ubStr, 0x00, 63);
    cp2130_get_manufacturer_string(spi, ubStr);
    printf("Manufacturer String: %s\n\r", ubStr);
    memset(ubStr, 0x00, 63);
    cp2130_get_prod_string(spi, ubStr);
    printf("Product String: %s\n\r", ubStr);
    memset(ubStr, 0x00, 63);
    cp2130_get_serial(spi, ubStr);
    printf("Serial: %s\n\r", ubStr);

    /*
    uint8_t ubPinCfg[20];
    cp2130_get_pin_cfg(spi, ubPinCfg);
    for(uint8_t i = 0; i < 11; i++)
    {
        printf("GPIO%d OTP ROM cfg: 0x%02X\n\r", i, ubPinCfg[i]);
    }*/

    cp2130_set_gpio_mode_level(spi, CP2130_GPIO0, CP2130_GPIO_OUT_PP, CP2130_GPIO_HIGH);
    //cp2130_set_gpio_mode_level(spi, CP2130_GPIO5, CP2130_GPIO_OUT_PP, CP2130_GPIO_LOW);
    //cp2130_set_gpio_mode_level(spi, CP2130_GPIO7, CP2130_GPIO_OUT_PP, CP2130_GPIO_LOW);

    //cp2130_set_gpio_values(spi, 0x00, CP2130_GPIO7_MSK);

    cp2130_set_event_counter(spi, CP2130_EVNT_CNT_FALLING_EDG, 0);

    cp2130_set_clockdiv(spi, 3); // 24 MHz / 3 = 8MHz

    cp2130_set_spi_word(spi, CP2130_SPI_CH0, CP2130_SPI_WRD_MODE3 | CP2130_SPI_WRD_CS_MODE_PP | CP2130_SPI_WRD_CLK_750K);

    cp2130_set_gpio_cs(spi, CP2130_CS_CH0, CP2130_CS_MD_EN_DIS_OTHERS);

    //sleep(5);

    uint8_t ubEvntMd;
    uint16_t ubCount;
    cp2130_get_event_counter(spi, &ubEvntMd, &ubCount);
    printf("Event Counter: %d\n\r\n\r", ubCount);

    tmc4671_init(spi);

    printf("Chip info:\n\r");

    tmc4671_write(TMC4671_CHIPINFO_ADDR, TMC4671_CHIPINFO_ADDR_SI_TYPE);
    uint32_t ulSiType = tmc4671_read(TMC4671_CHIPINFO_DATA);
    printf("SI Type: %c%c%c%c\n\r", (ulSiType >> 24) & 0xFF, (ulSiType >> 16) & 0xFF, (ulSiType >> 8) & 0xFF, ulSiType & 0xFF);

    tmc4671_write(TMC4671_CHIPINFO_ADDR, TMC4671_CHIPINFO_ADDR_SI_VERSION);
    uint32_t ulVersion = tmc4671_read(TMC4671_CHIPINFO_DATA);
    printf("SI Version: %hu.%hu\n\r\n\r", (ulVersion >> 16) & 0xFF, ulVersion & 0xFF);
/*
    for(uint8_t i = 0x00; i < 0x7D; i++)
    {
        printf("0x%02X: %08X\n\r", i,tmc4671_read(i));
    }
*/
    printf("\n\rPWM freq: %huHz\n\r", tmc4671_get_PWM_freq());
    printf("ENABLE_IN: %d\n\r", !!(tmc4671_read(TMC4671_INPUTS_RAW) & TMC4671_ENABLE_IN_RAW_MASK));

    printf("STATUS_FLAGS: %08X\n\r\n\r", tmc4671_read(TMC4671_STATUS_FLAGS));

    printf("VM adc raw: %08X\n\r", tmc4671_get_adc_raw(TMC4671_ADC_RAW_ADDR_ADC_AGPI_A_RAW_ADC_VM_RAW));
    printf("Motor Voltage: %.2f V\n\r", tmc4671_get_vm_v());

    // Type of motor &  PWM configuration
    printf("Type of motor &  PWM configuration\n\r");
    tmc4671_set_pole_pairs(1);
    tmc4671_set_motor_type(TMC4671_SINGLE_PHASE_DC_MOTOR);
    tmc4671_set_pwm_polarity(0, 0);
    tmc4671_set_PWM_freq(50000);
	tmc4671_set_dead_time(20, 20);
    tmc4671_enable_PWM();

    // ADC configuration
    printf("ADC configuration\n\r");
    tmc4671_write(TMC4671_dsADC_MDEC_B_MDEC_A, 0x00A500A5); // Decimation configuration register.
    tmc4671_modify(TMC4671_DS_ANALOG_INPUT_STAGE_CFG, (4 << TMC4671_ADC_VM_SHIFT), TMC4671_ADC_VM_MASK);
	tmc4671_modify(TMC4671_dsADC_MCFG_B_MCFG_A, 0x00100010, TMC4671_SEL_NCLK_MCLK_I_A_MASK | TMC4671_SEL_NCLK_MCLK_I_B_MASK);
	tmc4671_write(TMC4671_dsADC_MCLK_A, 0x20000000);
	tmc4671_write(TMC4671_dsADC_MCLK_B, 0x00000000);

    //ADC scale & offset
    //tmc4671_write(TMC4671_ADC_I_SELECT, (0 & TMC4671_ADC_I0_SELECT_MASK) | ((1 << TMC4671_ADC_I1_SHIFT) & TMC4671_ADC_I1_SELECT_MASK) | ((0 << TMC4671_ADC_I_UX_SELECT_SHIFT) & TMC4671_ADC_I_UX_SELECT_MASK) | ((2 << TMC4671_ADC_I_V_SELECT_SHIFT) & TMC4671_ADC_I_V_SELECT_MASK) | ((1 << TMC4671_ADC_I_WY_SELECT_SHIFT) & TMC4671_ADC_I_WY_SELECT_MASK));
    tmc4671_write(TMC4671_ADC_I_SELECT, 0x1400030);

    printf("ADC scale & offset\n\r");
    tmc4671_write(TMC4671_ADC_I0_SCALE_OFFSET, (tmc4671_get_I0_raw() & TMC4671_ADC_I0_OFFSET_MASK) | (((int16_t)(360) << TMC4671_ADC_I0_SCALE_SHIFT) & TMC4671_ADC_I0_SCALE_MASK));
    tmc4671_write(TMC4671_ADC_I1_SCALE_OFFSET, (tmc4671_get_I1_raw() & TMC4671_ADC_I1_OFFSET_MASK) | (((int16_t)(360) << TMC4671_ADC_I1_SCALE_SHIFT) & TMC4671_ADC_I1_SCALE_MASK));

    printf("raw adc I0: %d\n\r", tmc4671_get_I0_raw());
    printf("raw adc I0(V): %.0f mV\n\r", (float)tmc4671_get_I0_raw() * 0.076295109f);
    printf("scaled adc IUX: %d\n\r", (int16_t)(tmc4671_read(TMC4671_ADC_IWY_IUX) & TMC4671_ADC_IUX_MASK));


    printf("raw adc I1: %d\n\r", tmc4671_get_I1_raw());
    printf("raw adc I1(V): %.0f mV\n\r", (float)tmc4671_get_I1_raw() * 0.076295109f);
    printf("scaled adc IWY: %d\n\r", (int16_t)((tmc4671_read(TMC4671_ADC_IWY_IUX) & TMC4671_ADC_IWY_MASK) >> TMC4671_ADC_IWY_SHIFT));

    printf("scaled adc IV: %d\n\r", (int16_t)(tmc4671_read(TMC4671_ADC_IV) & TMC4671_ADC_IV_MASK));

	// Encoder configuration
    printf("Encoder configuration\n\r");
	tmc4671_write(TMC4671_ABN_DECODER_MODE, 0x00000000); // Control bits how to handle ABN decoder signals.
	tmc4671_write(TMC4671_ABN_DECODER_PPR, 1024);
	tmc4671_write(TMC4671_ABN_DECODER_COUNT, 0x00000000);
	tmc4671_write(TMC4671_ABN_DECODER_PHI_E_PHI_M_OFFSET, 0x00000000);

    // set limits
    printf("set limits\n\r");
    tmc4671_set_uq_ud_limit(23767); // 23767
    tmc4671_set_torque_flux_limit(10000);
    tmc4671_set_accelaration_limit(5000);
    tmc4671_set_velocity_limit(10000);

    // selections
    printf("selections\n\r");
	tmc4671_write(TMC4671_VELOCITY_SELECTION, 2);  // phi_m_abn
	tmc4671_write(TMC4671_POSITION_SELECTION, 2);  // phi_m_abn

    // set PI parameter
    printf("set PI parameter\n\r");
    tmc4671_set_torque_flux_PI(1000, 0);  // P and I parameter for the flux regulator and for the torque regulator.
    tmc4671_set_velocity_PI(1000, 0);    // P and I parameter for the velocity regulator.
    tmc4671_set_position_PI(1000, 0);     // P parameter for the position regulator.

    // init encoder
    printf("init encoder\n\r");
    tmc4671_switch_motion_mode(TMC4671_MOTION_MODE_UQ_UD_EXT);
    tmc4671_write(TMC4671_ABN_DECODER_PHI_E_PHI_M_OFFSET, 0x00000000);
    tmc4671_write(TMC4671_PHI_E_SELECTION, TMC4671_PHI_E_EXT);
    tmc4671_write(TMC4671_PHI_E_EXT, 0x00000000);
    tmc4671_write(TMC4671_UQ_UD_EXT, 32767);
    //sleep(5);

    // clear abn decoder count
    //printf("clear abn decoder count\n\r");
    //tmc4671_write(TMC4671_ABN_DECODER_COUNT, 0x00000000);

    // feedback selection
    //printf("feedback selection\n\r");
    //tmc4671_write(TMC4671_PHI_E_SELECTION, TMC4671_PHI_E_SELECTION_PHI_E_ABN);
    //tmc4671_write(TMC4671_VELOCITY_SELECTION, TMC4671_VELOCITY_PHI_M_ABN);

    // switch to torque mode
    //printf("switch to torque mode\n\r");
    //tmc4671_switch_motion_mode(TMC4671_MOTION_MODE_UQ_UD_EXT);

    // rotate right
    //printf("rotate right\n\r");tmc4671_write(TMC4671_UQ_UD_EXT, 4294967295);
    //sleep(2);

    // rotate left
    //printf("rotate left\n\r");
    //tmc4671_write(TMC4671_PID_TORQUE_FLUX_TARGET, 0xFC180000);
    //sleep(2);

    // stop
    //printf("stop\n\r");
    //tmc4671_write(TMC4671_PID_TORQUE_FLUX_TARGET, 0x00000000);

/*
    tmc4671_switch_motion_mode(TMC4671_MOTION_MODE_UQ_UD_EXT);
    tmc4671_write(TMC4671_UQ_UD_EXT, 3000 & TMC4671_UD_EXT_MASK);
    tmc4671_write(TMC4671_OPENLOOP_VELOCITY_TARGET, 10);
    tmc4671_write(TMC4671_OPENLOOP_ACCELERATION, 5);

    tmc4671_write(TMC4671_PHI_E_SELECTION, TMC4671_PHI_E_SELECTION_PHI_E_OPENLOOP);

    tmc4671_update_phi_selection_and_initialize(TMC4671_PHI_E_SELECTION_PHI_E_OPENLOOP);

    printf("\n\rTMC4671_ABN_DECODER_PHI_E_PHI_M_OFFSET %d\n\r", tmc4671_read(TMC4671_ABN_DECODER_PHI_E_PHI_M_OFFSET));

    printf("\n\ropen loop velocity actual %d\n\r", tmc4671_read(TMC4671_OPENLOOP_VELOCITY_ACTUAL));
    printf("\n\rPHI_E %d\n\r", tmc4671_read(TMC4671_PHI_E));
    printf("\n\rTMC4671_PID_FLUX_P_FLUX_I %d\n\r", tmc4671_read(TMC4671_PID_FLUX_P_FLUX_I));
    printf("\n\rTMC4671_PID_VELOCITY_TARGET %d\n\r", tmc4671_read(TMC4671_PID_VELOCITY_TARGET));
*/
    FILE *fp;

    fp = fopen("./tests/currents.csv", "w");

    if(!fp)
    {
        gxKeepRunning = 0;

        printf("could not open file.\n\r");
    }
    else
    {
        fprintf(fp, "I0:I1:I2:PHI_E\n\r");
    }

    gxKeepRunning = 1;

    while(gxKeepRunning)
    {
        printf("/----------------------------------/\n\r");
        printf("raw adc I0: %d\n\r", tmc4671_get_I0_raw());
        printf("raw adc I0(V): %.0f mV\n\r", (float)tmc4671_get_I0_raw() * 0.076295109f);
        printf("raw adc I1: %d\n\r", tmc4671_get_I1_raw());
        printf("raw adc I1(V): %.0f mV\n\r", (float)tmc4671_get_I1_raw() * 0.076295109f);
        printf("scaled adc IUX: %d mA\n\r", (int16_t)(tmc4671_read(TMC4671_ADC_IWY_IUX) & TMC4671_ADC_IUX_MASK));
        printf("scaled adc IV: %d mA\n\r",  (int16_t)(tmc4671_read(TMC4671_ADC_IV) & TMC4671_ADC_IV_MASK));
        printf("scaled adc IWY: %d mA\n\r",  (int16_t)((tmc4671_read(TMC4671_ADC_IWY_IUX) & TMC4671_ADC_IWY_MASK) >> TMC4671_ADC_IWY_SHIFT));

        printf("position: %d", tmc4671_read(TMC4671_ABN_DECODER_COUNT));

        sleep(1);

        //fprintf(fp, "%d:%d:%d:%d\n\r", (int16_t)(tmc4671_read(TMC4671_ADC_IWY_IUX) & TMC4671_ADC_IUX_MASK), (int16_t)(tmc4671_read(TMC4671_ADC_IV) & TMC4671_ADC_IV_MASK), (int16_t)((tmc4671_read(TMC4671_ADC_IWY_IUX) & TMC4671_ADC_IWY_MASK) >> TMC4671_ADC_IWY_SHIFT), tmc4671_read(TMC4671_ABN_DECODER_COUNT) & TMC4671_ABN_DECODER_COUNT_MASK);
        //fprintf(fp, "%d:%d:0:%d\n\r", tmc4671_get_I0_raw(), tmc4671_get_I1_raw(), tmc4671_read(TMC4671_PHI_E));
    }

    printf("leaving...\n\r");

    if(fp)
        fclose(fp);


    cp2130_free(spi);

	if(ctx)
		libusb_exit(ctx);

    return EXIT_SUCCESS;
}

void sig_handler(int signo)
{
    gxKeepRunning = 0;
}

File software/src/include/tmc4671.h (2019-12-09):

#ifndef __TMC4671_H
#define __TMC4671_H

#include <stdio.h>
#include <stdint.h>
#include <stdlib.h>
#include <unistd.h>
#include <time.h>
#include "cp2130.h"

// TMC4671 Frame
#define TMC4671_FRAME_WRITE     0x80
#define TMC4671_FRAME_READ      0x00

// TMC4671 Register Address
#define TMC4671_CHIPINFO_DATA                      0x00
#define TMC4671_CHIPINFO_ADDR                      0x01

#define TMC4671_ADC_RAW_DATA                       0x02
#define TMC4671_ADC_RAW_ADDR                       0x03

#define TMC4671_dsADC_MCFG_B_MCFG_A                0x04
#define TMC4671_dsADC_MCLK_A                       0x05
#define TMC4671_dsADC_MCLK_B                       0x06
#define TMC4671_dsADC_MDEC_B_MDEC_A                0x07

#define TMC4671_ADC_I1_SCALE_OFFSET                0x08
#define TMC4671_ADC_I0_SCALE_OFFSET                0x09
#define TMC4671_ADC_I_SELECT                       0x0A
#define TMC4671_ADC_I1_I0_EXT                      0x0B

#define TMC4671_DS_ANALOG_INPUT_STAGE_CFG          0x0C

#define TMC4671_AENC_0_SCALE_OFFSET                0x0D
#define TMC4671_AENC_1_SCALE_OFFSET                0x0E
#define TMC4671_AENC_2_SCALE_OFFSET                0x0F

#define TMC4671_AENC_SELECT                        0x11

#define TMC4671_ADC_IWY_IUX                        0x12
#define TMC4671_ADC_IV                             0x13
#define TMC4671_AENC_WY_UX                         0x15
#define TMC4671_AENC_VN                            0x16

#define TMC4671_PWM_POLARITIES                     0x17
#define TMC4671_PWM_MAXCNT                         0x18
#define TMC4671_PWM_BBM_H_BBM_L                    0x19
#define TMC4671_PWM_SV_CHOP                        0x1A
#define TMC4671_MOTOR_TYPE_N_POLE_PAIRS            0x1B

#define TMC4671_PHI_E_EXT                          0x1C
#define TMC4671_PHI_M_EXT                          0x1D
#define TMC4671_POSITION_EXT                       0x1E
#define TMC4671_OPENLOOP_MODE                      0x1F
#define TMC4671_OPENLOOP_ACCELERATION              0x20
#define TMC4671_OPENLOOP_VELOCITY_TARGET           0x21
#define TMC4671_OPENLOOP_VELOCITY_ACTUAL           0x22
#define TMC4671_OPENLOOP_PHI                       0x23
#define TMC4671_UQ_UD_EXT                          0x24

#define TMC4671_ABN_DECODER_MODE                   0x25
#define TMC4671_ABN_DECODER_PPR                    0x26
#define TMC4671_ABN_DECODER_COUNT                  0x27
#define TMC4671_ABN_DECODER_COUNT_N                0x28
#define TMC4671_ABN_DECODER_PHI_E_PHI_M_OFFSET     0x29
#define TMC4671_ABN_DECODER_PHI_E_PHI_M            0x2A

#define TMC4671_ABN_2_DECODER_MODE                 0x2C
#define TMC4671_ABN_2_DECODER_PPR                  0x2D
#define TMC4671_ABN_2_DECODER_COUNT                0x2E
#define TMC4671_ABN_2_DECODER_COUNT_N              0x2F
#define TMC4671_ABN_2_DECODER_PHI_M_OFFSET         0x30
#define TMC4671_ABN_2_DECODER_PHI_M                0x31

#define TMC4671_HALL_MODE                          0x33
#define TMC4671_HALL_POSITION_060_000              0x34
#define TMC4671_HALL_POSITION_180_120              0x35
#define TMC4671_HALL_POSITION_300_240              0x36
#define TMC4671_HALL_PHI_E_PHI_M_OFFSET            0x37
#define TMC4671_HALL_DPHI_MAX                      0x38
#define TMC4671_HALL_PHI_E_INTERPOLATED_PHI_E      0x39
#define TMC4671_HALL_PHI_M                         0x3A

#define TMC4671_AENC_DECODER_MODE                  0x3B
#define TMC4671_AENC_DECODER_N_MASK_N_THRESHOLD    0x3C
#define TMC4671_AENC_DECODER_PHI_A_RAW             0x3D
#define TMC4671_AENC_DECODER_PHI_A_OFFSET          0x3E
#define TMC4671_AENC_DECODER_PHI_A                 0x3F

#define TMC4671_AENC_DECODER_PPR                   0x40
#define TMC4671_AENC_DECODER_COUNT                 0x41
#define TMC4671_AENC_DECODER_COUNT_N               0x42
#define TMC4671_AENC_DECODER_PHI_E_PHI_M_OFFSET    0x45
#define TMC4671_AENC_DECODER_PHI_E_PHI_M           0x46
#define TMC4671_AENC_DECODER_POSITION              0x47

#define TMC4671_PIDIN_TORQUE_TARGET_FLUX_TARGET    0x4A
#define TMC4671_PIDIN_VELOCITY_TARGET              0x4B
#define TMC4671_PIDIN_POSITION_TARGET              0x4C

#define TMC4671_CONFIG_DATA                        0x4D
#define TMC4671_CONFIG_ADDR                        0x4E

#define TMC4671_VELOCITY_SELECTION                 0x50
#define TMC4671_POSITION_SELECTION                 0x51
#define TMC4671_PHI_E_SELECTION                    0x52
#define TMC4671_PHI_E                              0x53

#define TMC4671_PID_FLUX_P_FLUX_I                  0x54
#define TMC4671_PID_TORQUE_P_TORQUE_I              0x56
#define TMC4671_PID_VELOCITY_P_VELOCITY_I          0x58
#define TMC4671_PID_POSITION_P_POSITION_I          0x5A
#define TMC4671_PID_TORQUE_FLUX_TARGET_DDT_LIMITS  0x5C
#define TMC4671_PIDOUT_UQ_UD_LIMITS                0x5D
#define TMC4671_PID_TORQUE_FLUX_LIMITS             0x5E
#define TMC4671_PID_ACCELERATION_LIMIT             0x5F
#define TMC4671_PID_VELOCITY_LIMIT                 0x60
#define TMC4671_PID_POSITION_LIMIT_LOW             0x61
#define TMC4671_PID_POSITION_LIMIT_HIGH            0x62

#define TMC4671_MODE_RAMP_MODE_MOTION              0x63
#define TMC4671_PID_TORQUE_FLUX_TARGET             0x64
#define TMC4671_PID_TORQUE_FLUX_OFFSET             0x65
#define TMC4671_PID_VELOCITY_TARGET                0x66
#define TMC4671_PID_VELOCITY_OFFSET                0x67
#define TMC4671_PID_POSITION_TARGET                0x68

#define TMC4671_PID_TORQUE_FLUX_ACTUAL             0x69
#define TMC4671_PID_VELOCITY_ACTUAL                0x6A
#define TMC4671_PID_POSITION_ACTUAL                0x6B

#define TMC4671_PID_ERROR_DATA                     0x6C
#define TMC4671_PID_ERROR_ADDR                     0x6D
#define TMC4671_INTERIM_DATA                       0x6E
#define TMC4671_INTERIM_ADDR                       0x6F

#define TMC4671_WATCHDOG_CFG                       0x74
#define TMC4671_ADC_VM_LIMITS                      0x75
#define TMC4671_INPUTS_RAW                         0x76
#define TMC4671_OUTPUTS_RAW                        0x77

#define TMC4671_STEP_WIDTH                         0x78

#define TMC4671_UART_BPS                           0x79
#define TMC4671_UART_ADDRS                         0x7A

#define TMC4671_GPIO_dsADCI_CONFIG                 0x7B

#define TMC4671_STATUS_FLAGS                       0x7C
#define TMC4671_STATUS_MASK                        0x7D

// motion modes
#define TMC4671_MOTION_MODE_STOPPED     0
#define TMC4671_MOTION_MODE_TORQUE      1
#define TMC4671_MOTION_MODE_VELOCITY    2
#define TMC4671_MOTION_MODE_POSITION    3
#define TMC4671_MOTION_MODE_UQ_UD_EXT   8
#define TMC4671_MOTION_MODE_MINI_MOVE   9

// phi_e selections
#define TMC4671_PHI_E_EXTERNAL   1
#define TMC4671_PHI_E_OPEN_LOOP  2
#define TMC4671_PHI_E_ABN        3
#define TMC4671_PHI_E_HALL       5
#define TMC4671_PHI_E_AENC       6
#define TMC4671_PHI_A_AENC       7
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

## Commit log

2019-03-24 Started Documentation and sch
    [motor-constant-comparisson.xlsx, rough-budget.xlsx, v0a.sch]
2019-03-25 rough schematic and component requirement defenition
    [rough-budget.xlsx, v0a.sch]
2019-03-27 changed current sense resistors to 700u
    [motor-specs.xlsx, rough-budget.xlsx, v0a.sch]
2019-03-27 sch work
    [v0a.sch]
2019-03-29 pcb work
    [v0a.brd, v0a.sch]
2019-04-01 pcb 80% finished
    [servo-ctrl.brd, servo-ctrl.sch, v0a.brd]
2019-04-03 finished pcb, added pdf and png exports of pcb
    [servo-ctrl.brd, servo-ctrl.sch]
2019-04-04 component request preparation
    [rough-budget.xlsx, servo-ctrl.brd, servo-ctrl.sch]
2019-04-04 component request
    [rough-budget.xlsx, servo-ctrl.brd, servo-ctrl.sch]
2019-04-05 bom component request
    [bom-component-request.xlsx]
2019-04-05 request changes
    [bom-component-request.xlsx, servo-ctrl.brd, servo-ctrl.sch]
2019-05-15 added tagconnect to bom
    [bom-component-request.xlsx, fmc.brd, fmc.sch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]
2019-05-15 fixed bom inconsintency
    [bom-component-request.xlsx]
2019-05-28 tmc4671 api work
    [fmc.brd]
2019-06-05 workin BOI
    [fmc.brd, fmc.sch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]
2019-06-06 please work for the love of god
    [currents.csv]
2019-06-11 feedback testing
    [currents.csv]
2019-06-14 ft4222h breakout
    [fmc.brd, fmc.sch, ft4222h.brd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]
2019-12-09 fixed current measuring, still can't make it work
    [main.c, tmc4671.h]

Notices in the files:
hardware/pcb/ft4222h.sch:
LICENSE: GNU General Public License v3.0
